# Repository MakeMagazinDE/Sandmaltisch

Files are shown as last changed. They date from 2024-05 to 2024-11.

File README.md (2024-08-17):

GitHub Logo

Maker Media GmbH

***

# Der IKEA-Hack Sandmaltisch

**Nach dem Erfahrungsbericht über den Bau des Sandtisches wollten viele Leser mehr wissen und der Ruf nach einer kompletten Bauanleitung wurde laut. Hier ist sie! Unser Autor hat keine Mühen gescheut und neben diesem Übersichtsartikel eine ausführliche Online-Schritt-für-Schritt-Anleitung, Stücklisten und CAD-Zeichnungen angefertigt.**

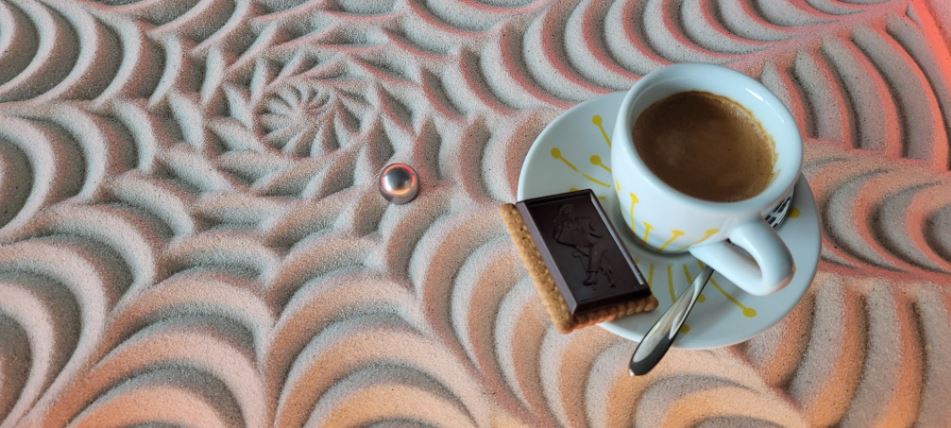
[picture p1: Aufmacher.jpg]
 

Den vollständigen Artikel gibt es in der [Make 4/24 ab Seite 16](https://www.heise.de/ratgeber/Ikea-Sandmaltisch-Bauanleitung-Teil-1-Material-und-Zusammenbau-9773244.html).

Hier finden Sie die Schritt-für-Schritt Anleitung, die 3D-Druckteile, die Firmware und GCODE-Beispielbilder.

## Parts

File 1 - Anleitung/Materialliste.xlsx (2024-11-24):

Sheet: Materialliste
IKEA Lack Sandmaltisch
Materialliste |  |  |  |  |  | 2024-11-24
Anzahl | Produkt | Total | Lieferant | Link | Hinweis | Status
1 | Makerbase MKS DLC32, ESP32 WIFI Board V2.1, inkl. zwei TMC2208 Treiber und Kühlkörper | EUR 18.00 | AliMakerstore | https://de.aliexpress.com/item/1005003246859709.html | Im Kit sind drei TMC2208-Treiber dabei. Wir brauchen nur zwei davon.
1 | Speicherkarte SD, 16 GB | EUR 5.00 | Digital-Factory Store | https://de.aliexpress.com/item/1005005834105747.html | Auf der Speicherkarte werden die GCODE-Dateien gespeichert. Geringe Anforderungen an die Speicherkapazität und Performance.
3 | Stepper Motoren NEMA17, Pancake 17HS4023, inkl. Kabel 1 Meter | EUR 15.00 | SINGRLIGOD Store | https://de.aliexpress.com/item/1005003173049902.html
2 | Limit Switches, ZW12-B | EUR 1.00 | ZHRIVOER CHINA Store | https://de.aliexpress.com/item/10000284039075.html | ZW12-B empfohlen. Bei anderen Schaltern muss sonst die Auslöseposition nachjustiert werden.
1 | Kippschalter Rocker KCD1-101 | EUR 1.00 | WGXCPP Muhao Online Store | https://de.aliexpress.com/item/1005001724551095.html | Wird für Ein-/Ausschalter verwendet.
1 | Momentary Push Button, R13-507 | EUR 1.00 | WGXCPP Muhao Online Store | https://de.aliexpress.com/item/1005001709481942.html | Wird für Reset-Schalter verwendet.
1 | 2-Pin Schraubterminal, 2.54 PCB | EUR 2.00 | E-Smartworld Store | https://de.aliexpress.com/item/1005001677869988.html | Für den Anschluss des Ein-/Ausschalters an den Controller.
2 | JST XH Stecker mit Kabel, 2 pin, 10cm | EUR 1.50 | SANDOMEY Store | https://de.aliexpress.com/item/1005001432733235.html | Für den Anschluss des Reset-Schalters an den Controller und für den Anschluss des StepDown-Converters an den 12/24-Ausgang des Controllers.
2 | JST XH Stecker mit Kabel, 3 pin, 10cm | EUR 1.50 | SANDOMEY Store | https://de.aliexpress.com/item/1005001432733235.html | Für den Anschluss der Limit Switches an den Controller.
1 | 2-Pin Kabel, AWG22, 2 Meter lang | EUR 3.00 | SkyCable Store | https://de.aliexpress.com/item/1005001732356744.html | Für den Anschluss des Ein-/Ausschalters an den Controller sowie für die Verbindung der Limit Switches mit dem Controller.
1 | Steckernetzteil, 12V, 3A, 36W, Power Jack 5.5 x 2.1mm | EUR 20.00 | (Diverse) | https://www.amazon.de/Stromversorgung-Lichtstreifen-Fernseher-Verst%C3%A4rker-Transformator-12V-3A/dp/B0BP66JZLX | Oder ein beliebiges Netzteil 12-24V, 2-3A. Möglichst langes, schwarzes Kabel empfohlen.
2 | Linearstangen zylindrisch, 8mm, 800mm, inkl. 4xLM8UU Lager | EUR 22.00 | ZHUHAI Store | https://de.aliexpress.com/item/1005001682267073.html | Von den LM8UU-Lagern werden nur 2 benötigt.
2 | Linearstangen zylindrisch, 8mm, 500mm, inkl. 4xLM8LUU Lager | EUR 21.00 | ZHUHAI Store | https://de.aliexpress.com/item/1005001682564147.html | Von den LM8LUU-Lagern werden nur 2 benötigt.
1 | GT2 Kit: 5m Zahnriemen 6mm, 2x Idler, 2x Pulleys | EUR 4.00 | SINGRLIGOD Store | https://de.aliexpress.com/item/1005003025464689.html
1 | GT2 Pulley, 20T W6 B5 | EUR 1.00 | SINGRLIGOD Store | https://de.aliexpress.com/item/1005002425542670.html
1 | GT2 Idler, 20 Zähne, 5mm Bohrung | EUR 1.00 | Big Tree Tech | https://de.aliexpress.com/item/33062594983.html
2 | GT2 Aluminium Klemmen | EUR 2.00 | Super 3D Technology | https://de.aliexpress.com/item/32813654055.html
1 | Kugel 20mm, massiv, ferromagnetisch, rostfrei | EUR 2.00 | GLT SMT Store | https://de.aliexpress.com/item/1005002787243996.html | Alternativer Lieferant aus Deutschland, liefert rostfreie, polierte Kugeln: https://tinyurl.com/5n8bmydn
1 | Neodym Scheibenmagnet mit Loch zum Anschrauben, Ø25 x 7mm, N40 | EUR 4.00 | Magnethandel.de | https://www.magnethandel.de/neodym-ringmagnete-senkung-sued-25-55-7-mm | Der Magnet sollte eine Senkbohrung von mindestens 4mm aufweisen, damit die M4-Schraube durchpasst. Eine Lieferung in die Schweiz ist leider sehr teuer. Alternativer Lieferant: Supermagnete.ch
1 | Neodym Scheibenmagnet, Ø25 x 5mm, N35 | EUR 3.00 | Magnethandel.de | https://www.magnethandel.de/neodym-magnete-25-5-mm-n35
ca. 3.5kg | Dekorsand pasteurisiert, Körnung 0.1-0.6mm | EUR 10.00 | Baumarkt, Jumbo | https://www.jumbo.ch/de/gartenbau-technik/gartenbaumaterial/gartenbodenbelaege--mauern/sand--kies--splitt/farbsand/p/4206821
1 | Moosgummimatte, 50x100cm, 2mm Stärke, schwarz | EUR 5.00 | Netco Shop | https://netco-shop.de/product_info.php?products_id=301&MODsid=ivu8c33b531trk48m20c3l3pdq
1 | IKEA Lack, Couchtisch, 90x55, schwarzbraun | EUR 30.00 | Ikea | https://www.ikea.com/ch/de/p/lack-couchtisch-schwarzbraun-40104294/
1 | Spanplatte, 884x544x12mm, roh | EUR 5.00 | Hornbach |  | Dient als Zwischenplatte.
2 | Holzplatten, MDF, 80x550x3mm, roh | EUR 1.00 | Hornbach | https://www.hornbach.de/conf/duenn-mdf-platte-einseitig-schwarz-2440x1220x3-mm-zuschnitt-online-reservierbar/3820802/ | Die Holzplatten dienen zur seitlichen Abdeckung des technischen Zwischenbaus.
2 | Holzplatten, MDF, 80x893x3mm, roh | EUR 1.00 | Hornbach | https://www.hornbach.de/conf/duenn-mdf-platte-einseitig-schwarz-2440x1220x3-mm-zuschnitt-online-reservierbar/3820802/ | Die Holzplatten dienen zur seitlichen Abdeckung des technischen Zwischenbaus.
1 | Klebefolie d-c-fix, Blackwood, 67.5x200 cm | EUR 7.00 | Hornbach | https://www.hornbach.ch/de/p/d-c-fix-klebefolie-holzdekor-blackwood-67-5x200-cm/3829390/
2 | Kanthölzer, Fichte, 44x44x670mm | EUR 9.00 | Hornbach | https://www.hornbach.ch/de/p/konsta-kantholz-fichte-gehobelt-44x44x2500-mm/1001281/ | Kann aus einem Stück Kantholz Fichte 44x44x2500mm hergestellt werden. Dienen zur Befestigung der 3D gedruckten LED- und Glasscheibenhalter.
2 | Kanthölzer, Fichte, 44x44x330mm |  |  |  | Kann aus einem Stück Kantholz Fichte 44x44x2500mm hergestellt werden. Dienen zur Befestigung der 3D gedruckten LED- und Glasscheibenhalter.
1 | LED Profil LP7, 2 Meter | EUR 20.00 | Hornbach | https://www.hornbach.ch/de/p/led-lichtprofil-set-lp7-laenge-2-m-alufarben-fuer-led-streifen/6501809/ | In vier Teile zersägen: 2 x 670mm und 2 x 330mm
1 | LED Streifen, Paulmann Entertain LED, 3m, RGB, 5V, 60 LEDs/Meter, inkl. Fernbedienung | EUR 50.00 | Hornbach | https://www.hornbach.de/p/betriebsfertiger-entertain-led-stripe-3-0-m-dynamic-rgb-farbwechsel-180-leds-mit-memoryfunktion-fernbedienung-12v/10538125/
1 | DC Power Jack Kabel, männlich, 5.5x2.5mm, Länge ca. 1 Meter | EUR 1.00 | Bolantedz Official Store | https://de.aliexpress.com/item/1005004222908762.html
1 | StepDown Converter 5V, Mini560 | EUR 1.00 | TULX Global Store | https://de.aliexpress.com/item/1005004114708195.html
4 | LED Verbinder, 4 Pin, 10mm, double | EUR 2.00 | Loamlin Official Store | https://de.aliexpress.com/item/1005001521762588.html | Die Breite dieser Stecker ist 14.5mm. Breiter dürfen die Stecker keinesfalls sein!
1 | Sicherheitsglas ESG, 6mm Stärke, Kanten gesäumt | EUR 100.00 | Lokaler Glashändler oder Baumarkt | https://www.jumbo.ch/de/bauen-renovieren/glas-kunstglas/kunstglas/einscheibensicherheitsglas-esg-6-mm/p/5840845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 | Die genauen Abmessungen ergeben sich im Verlaufe des Projekts, siehe Anleitung (Richtwert: 418x768mm). Nach Möglichkeit "extraweiss" bestellen (ohne Grünstich).
1 | Saugnapf | EUR 2.00 | Homast Store | https://de.aliexpress.com/item/1005004833801393.html | Optional. Damit kann die Glasplatte aus der Versenkung gehoben werden.
 | Filament, PLA oder PETG, schwarz, ca. 1.2 kg | EUR 40.00
 | Kleinteile gemäss Register "Schrauben und Muttern" | EUR 30.00
 | Holzleim
 | Schrumpfschlauch
 | Isolierband
 | Schleifpapier grob
 |  | EUR 443.00

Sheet: Schrauben und Muttern
IKEA Lack Sandmaltisch
Schrauben und Muttern
Verbindung | Anzahl | Artikel | Abmessung | Empfehlung Kopf | Hinweis
Abdeckung an Eckteile | 8 | Metallschrauben, M3x10, schwarz, Ultraflachkopf | M3x10 | Ultraflachkopf | Schwarz und Flachkopf empfohlen, da sichtbare Schraube.
Abdeckung an Eckteile | 8 | Unterlegscheiben, M3x10, schwarz | M3x10 |  | Schwarz empfohlen, da sichtbare Unterlegscheibe.
Abdeckung an Eckteile | 8 | Gewindeeinsätze, M3xL5xOD4.5 | M3x5x4.5
Controller-Box: Rahmen an Controller-Boden | 2 | Metallschrauben, M3x10, schwarz, Ultraflachkopf | M3x10 | Ultraflachkopf | Als Achse für den Klapp-Mechanismus der Box.
Controller-Box: Rahmen an Controller-Boden | 1 | Gewindeeinsätze, M3xL5xOD4.5 | M3x5x4.5 |  | Für die Arretierung beim Auf-/Zuklappen.
Controller-Box: Rahmen an Controller-Boden | 1 | Metallschrauben, M3x6 | M3x6 |  | Für die Arretierung beim Auf-/Zuklappen.
Makerbase-Board in Controller-Box | 4 | Metallschrauben, M3x6 | M3x6 | Zylinder
Makerbase-Board in Controller-Box | 4 | Gewindeeinsätze, M3xL5xOD4.5 | M3x5x4.5
Controller-Box Rahmen an Zwischenplatte | 4 | Holzschrauben, 3x12, Senkkopf | 3x12 | Senkkopf | Schrauben sollten keinesfalls länger als 14mm sein.
Zwischenplatte an Tischbeine | 4 | Metallschraube, M6x50, Flachkopf | M6x50 | Flachrundkopf
Zwischenplatte an Tischbeine | 4 | Unterlegscheiben, M6x18x1.5 | M6x18
Eckteile an Verstrebungen | 8 | Metallschrauben, M5x25, Aussensechskant | M5x25 | Sechskant aussen
Eckteile an Verstrebungen | 8 | Unterlegscheiben M5x15x1 | M5x15x1
Eckteile an Verstrebungen | 8 | Sechskantmuttern, M5 | M5
Tischbeine an Verstrebungen | 4 | Holzschrauben, 3x12, Senkkopf | 3x12 | Senkkopf
Tischplatte mit Eckteilen | 4 | Gewindestift, M6x50, Innensechskant | M6x50 | Innensechskant | Diese Gewindestifte mit Innensechskant lassen sich mit einem Inbusschlüssel sehr gut einschrauben.
Tischplatte mit Eckteilen | 4 | Sechskantmuttern, M6 | M6
Tischplatte mit Eckteilen | 4 | Unterlegscheiben, M6x18x1.5 | M6x18
LED Profil-Halter an Rechteckleisten | 20 | Holzschrauben, 3x12, Senkkopf | 3x12 | Senkkopf
Y-Linearstangen an Anschlag-Plättchen | 2 | Gewindeeinsätze, M3xL5xOD4.5 | M3x5x4.5
Y-Linearstangen an Anschlag-Plättchen | 2 | Metallschrauben, M3x10 | M3x10 | Zylinder
Y-Linearstangen an Anschlag-Schraube | 2 | Metallschrauben, M3x10 | M3x10 | Zylinder
Montage NEMA17 Motor, X-Achse (Y-Schlitten) | 4 | Metallschrauben, M3x6 | M3x6 | Zylinder
Montage NEMA17 Motoren, Y-Achse | 6 | Metallschrauben, M3x6 | M3x6 | Zylinder | Drei Schrauben pro NEMA-Motor.
Montage GT2 Idler (X- und Y-Achsen) | 3 | Metallschrauben, M5x25, Ultraflachkopf | M5x25
Montage GT2 Idler X-Achse | 1 | Unterlegscheiben M5x15x1 | M5x15x1
Montage Lager auf Y-Achse mit Klemme | 8 | Metallschrauben, M3x10 | M3x10 | Zylinder
Montage Lager auf Y-Achse mit Klemme | 8 | Gewindeeinsätze, M3xL5xOD4.5 | M3x5x4.5
Arretierung Zahnriemen Y-Achsen mit Klemme | 2 | Metallschrauben, M3x10 | M3x10 | Zylinder
Arretierung Zahnriemen Y-Achsen mit Klemme | 2 | Gewindeeinsätze, M3xL5xOD4.5 | M3x5x4.5
Arretierung Zahnriemen Y-Achsen mit Schraube | 2 | Metallschrauben, M3x10 | M3x10 | Zylinder
Arretierung Zahnriemen Y-Achsen mit Schraube | 2 | Gewindeeinsätze, M3xL5xOD4.5 | M3x5x4.5
Montage Lager auf X-Achse mit Klemme | 2 | Metallschrauben, M3x20 | M3x20 | Zylinder
Montage Lager auf X-Achse mit Klemme | 2 | Gewindeeinsätze, M3xL5xOD4.5 | M3x5x4.5
Arretierung Zahnriemen X-Achse | 2 | Metallschrauben, M3x20 | M3x20 | Zylinder
Arretierung Zahnriemen X-Achse | 2 | Gewindeeinsätze, M3xL5xOD4.5 | M3x5x4.5
Montage Scheibenmagnet | 1 | Metallschrauben, M4x14, Senkkopf | M4x14 | Senkkopf | Senkkopf zwingend!
Montage Limit Schalter | 4 | Metallschrauben, M2.5x10 | M2.5x10 | Zylinder
Montage LED Kabel mit Kabelclips | 2 | Holzschrauben, 3x12, Senkkopf | 3x12 | Senkkopf
Ergebnis | 167
Total Schrauben und Muttern: | Anzahl | Link | AliExpress Shop | Status
Gewindeeinsätze, M3xL5xOD4.5 | 31 | https://de.aliexpress.com/item/1005006071488810.html | Edgar Gary
Gewindestift, M6x50, Innensechskant | 4 | https://de.aliexpress.com/item/1005003114146413.html | Haiking
Holzschrauben, 3x12, Senkkopf | 30 | https://de.aliexpress.com/item/1005002914051799.html | Zonsta
Metallschraube, M6x50, Flachkopf | 4 | https://de.aliexpress.com/item/1005004510618943.html | Haiking
Metallschrauben, M2.5x10 | 4 | https://de.aliexpress.com/item/1005004510631911.html | Haiking
Metallschrauben, M3x6 | 15 | https://de.aliexpress.com/item/1005003116411038.html | Haiking
Metallschrauben, M3x10, schwarz, Ultraflachkopf | 10 | https://de.aliexpress.com/item/1005004510624216.html | Haiking
Metallschrauben, M3x10 | 16 | https://de.aliexpress.com/item/1005003116411038.html | Haiking
Metallschrauben, M3x20 | 4 | https://de.aliexpress.com/item/1005003116557759.html | Haiking
Metallschrauben, M4x14, Senkkopf | 1 | https://de.aliexpress.com/item/1005004510637802.html | Haiking
Metallschrauben, M5x25, Ultraflachkopf | 3 | https://de.aliexpress.com/item/1005004510603548.html | Haiking
Metallschrauben, M5x25, Aussensechskant | 8 | https://de.aliexpress.com/item/1005003114095405.html | Haiking
Sechskantmuttern, M5 | 8 | https://de.aliexpress.com/item/1005003111431468.html | Haiking
Sechskantmuttern, M6 | 4 | https://de.aliexpress.com/item/1005003111431468.html | Haiking
Unterlegscheiben, M3x10, schwarz | 8 | https://de.aliexpress.com/item/1005003212029031.html | Blazingstar
Unterlegscheiben M5x15x1 | 9 | https://de.aliexpress.com/item/1005003226049975.html | Blazingstar
Unterlegscheiben, M6x18x1.5 | 8 | https://de.aliexpress.com/item/1005003226049975.html | Blazingstar
Summe | 167
Allgemeine Hinweise
Preis für alle Schrauben/Muttern insgesamt ca. 30 Euro.

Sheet: Druckbare Bauteile
IKEA Lack Sandmaltisch
Druckbare Bauteile
3MF-Datei | Druckzeit (h) | Gewicht (g) | Sichtbar | Filament | Hinweis
Verstrebungen.3mf | 1.30 | 36 | Ja | PLA Schwarz
Eckteile.3mf | 11.75 | 336 | Nein | PLA Rot
Tischbeinabdeckungen.3mf | 1.50 | 47 | Ja | PLA Schwarz
Kabelkanal.3mf | 1.00 | 26 | Nein | PLA Rot
Controller Box-Rahmen.3mf | 1.60 | 68 | Ja | PLA Schwarz
Controller Box-Boden.3mf | 2.00 | 76 | Ja | PLA Schwarz
Y-Schlitten.3mf | 3.50 | 64 | Nein | PLA Rot
X-Schlitten.3mf | 0.75 | 14 | Nein | PLA Rot
LED Profil-HalterEcken.3mf | 7.75 | 138 | Ja | PLA Schwarz
LED Profil-HalterStandard.3mf | 16.50 | 321 | Ja | PLA Schwarz | 3mf-Datei dreimal drucken (12 Stück)
LED Profil-Blenden.3mf | 0.75 | 16 | Ja | PLA Schwarz
Werkzeuge.3mf | 1.00 | 36 | Nein | PLA Blau
Kabelclip.3mf | 0.1 | 1 | Ja | PLA Schwarz
 | 49.50 | 1179

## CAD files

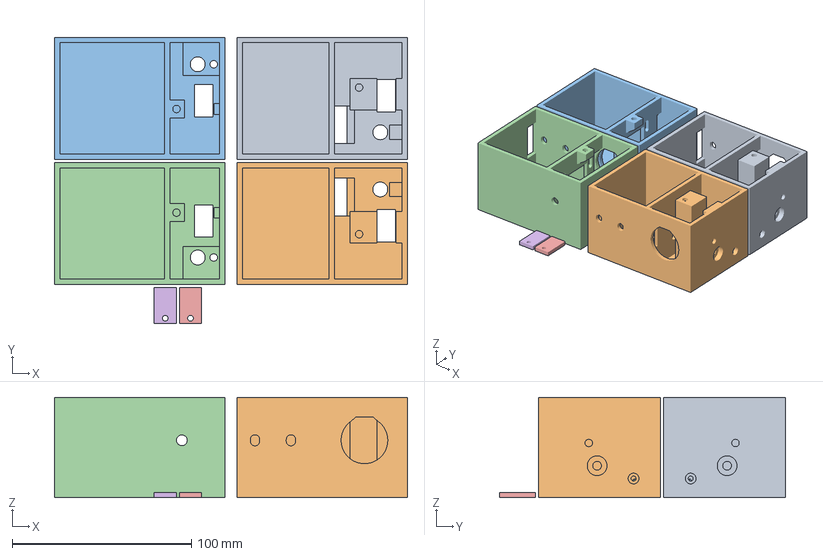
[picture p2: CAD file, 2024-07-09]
2 - 3D Druck/3MF-Dateien/Eckteile.3mf
196.8 x 159.6 x 56.0 mm
Eckteil 1-UntenLinks.stl
Eckteil 2-UntenRechts.stl
Eckteil 3-ObenLinks.stl
Eckteil 4-ObenRechts.stl
AnschlagZylinderstange.stl

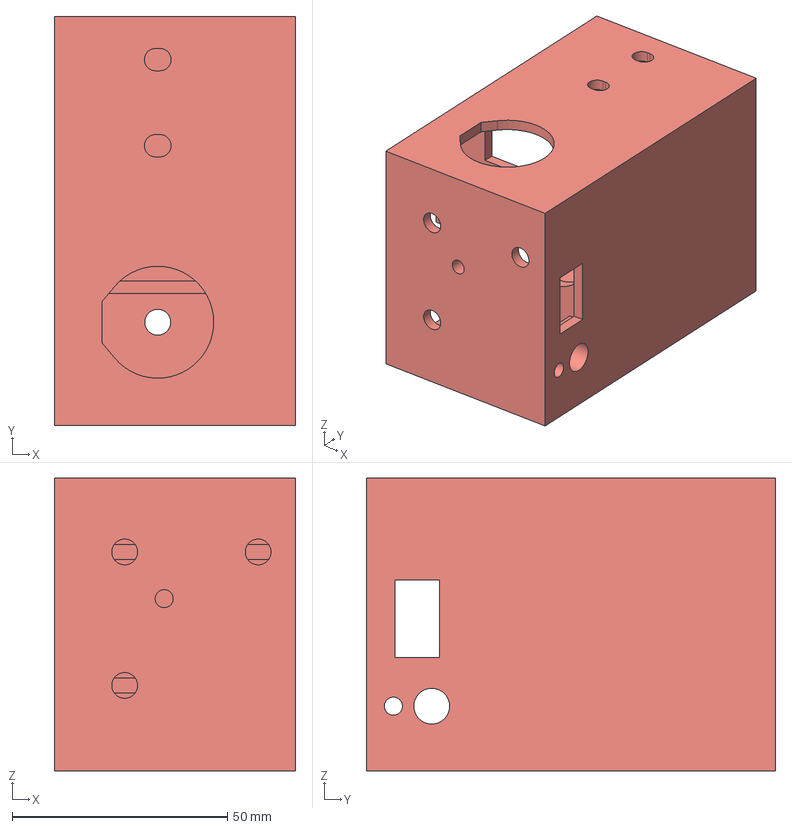
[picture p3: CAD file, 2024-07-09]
2 - 3D Druck/STEP-Dateien/Eckteil 4-ObenRechts.step
56.0 x 95.0 x 68.0 mm

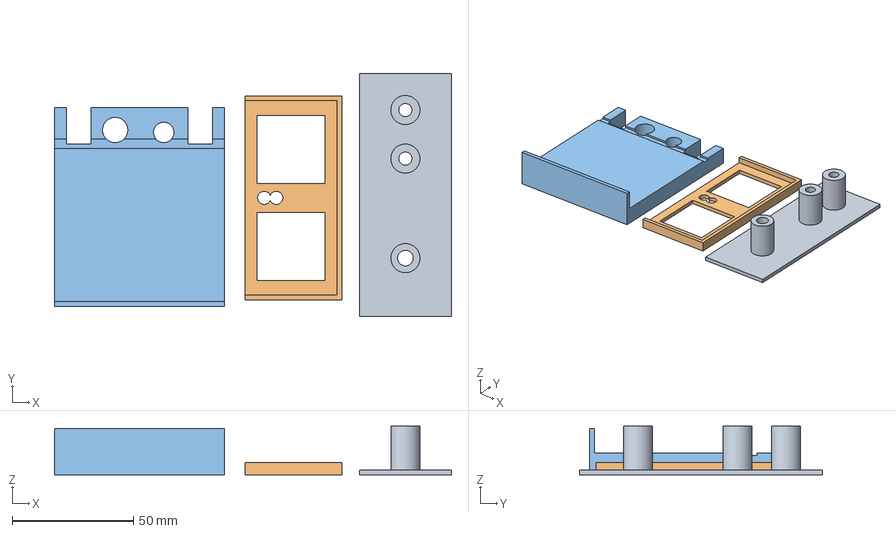
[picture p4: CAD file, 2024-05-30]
2 - 3D Druck/3MF-Dateien/Werkzeuge.3mf
163.5 x 100.0 x 20.0 mm
Bohrschablone Zwischenplatte.stl
Bohrschablone Abdeckung.stl
BohrschabloneLinealVollausschnitt.stl

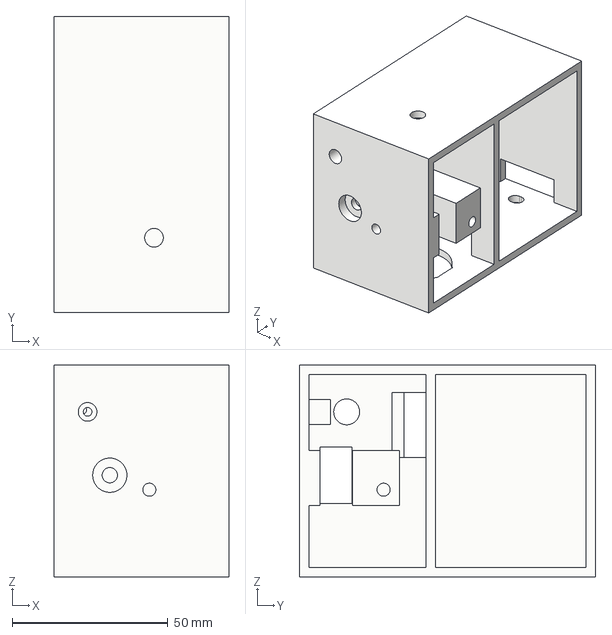
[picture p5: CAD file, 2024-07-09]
2 - 3D Druck/STEP-Dateien/Eckteil 1-UntenLinks.step
56.0 x 95.0 x 68.0 mm

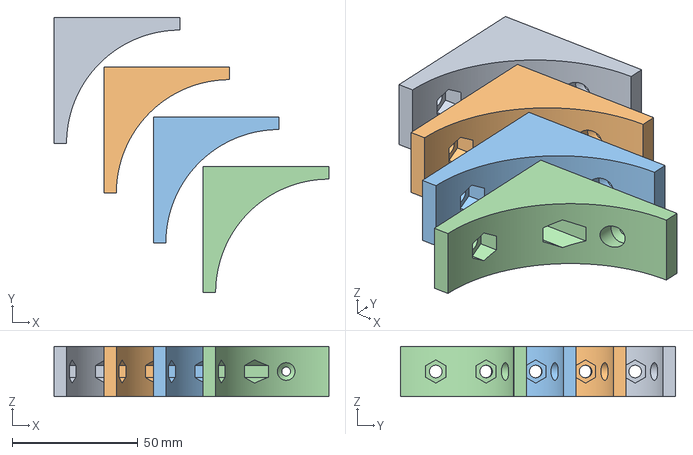
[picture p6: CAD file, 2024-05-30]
2 - 3D Druck/3MF-Dateien/Verstrebungen.3mf
109.2 x 109.2 x 20.0 mm

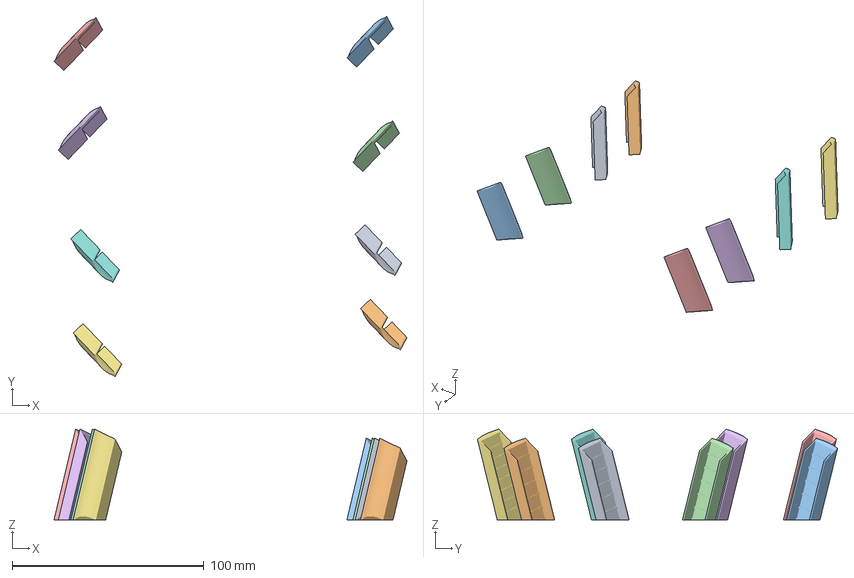
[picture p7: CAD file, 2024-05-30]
2 - 3D Druck/3MF-Dateien/LED Profil-Blenden.3mf
183.9 x 187.8 x 47.3 mm
LED ProfilBlende-EckeKurz1.stl
LED ProfilBlende-EckeKurz2.stl
LED ProfilBlende-EckeLang1.stl
LED ProfilBlende-EckeLang2.stl

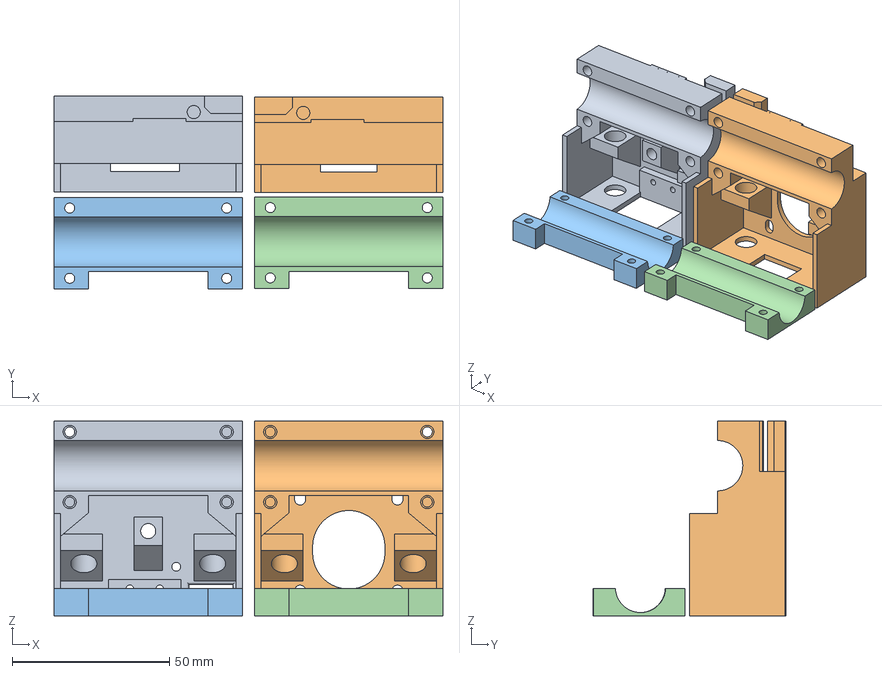
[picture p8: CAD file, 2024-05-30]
2 - 3D Druck/3MF-Dateien/Y-Schlitten.3mf
123.9 x 61.4 x 61.9 mm
Y-Schlitten 1-Links.stl
Y-Schlitten 2-Rechts.stl
Y-Schlitten-Klemme.stl

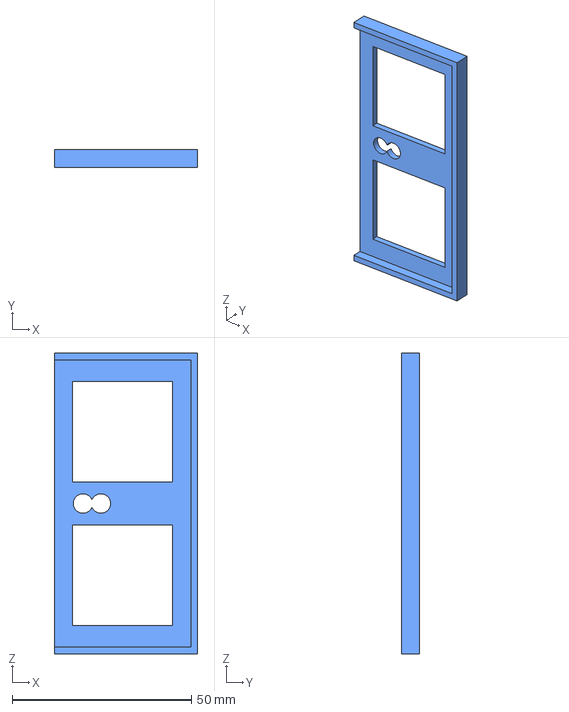
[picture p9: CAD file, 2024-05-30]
2 - 3D Druck/STEP-Dateien/Bohrschablone Abdeckung.step
40.0 x 5.00 x 84.0 mm

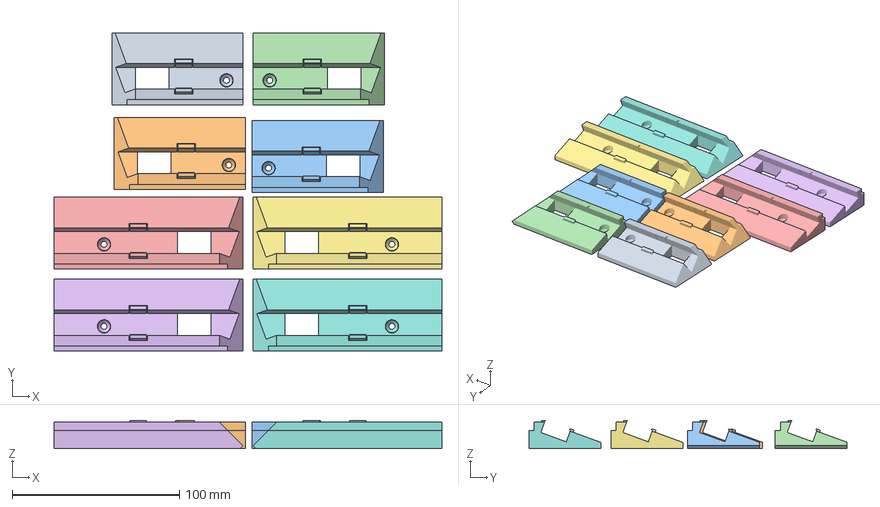
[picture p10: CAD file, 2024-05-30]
2 - 3D Druck/3MF-Dateien/LED Profil-HalterEcken.3mf
231.8 x 190.2 x 16.9 mm
LED Profil-HalterEckeKurz1.stl
LED Profil-HalterEckeKurz2.stl
LED Profil-HalterEckeLang1.stl
LED Profil-HalterEckeLang2.stl

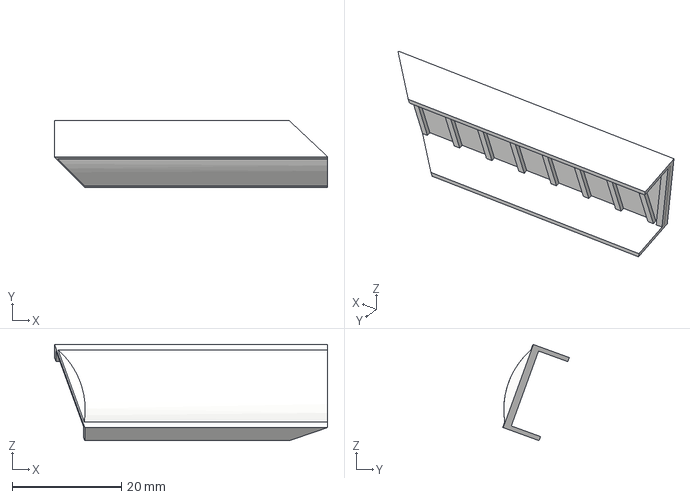
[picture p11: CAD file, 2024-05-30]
2 - 3D Druck/STEP-Dateien/LED ProfilBlende-EckeLang2.step
50.0 x 12.2 x 17.7 mm

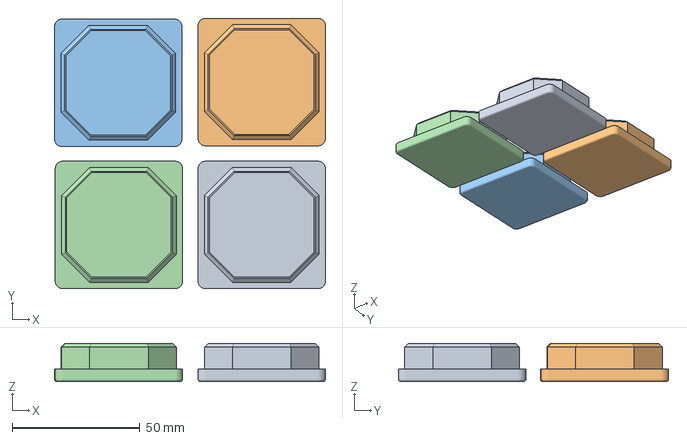
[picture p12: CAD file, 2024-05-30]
2 - 3D Druck/3MF-Dateien/Tischbeinabdeckungen.3mf
106.3 x 106.0 x 15.0 mm

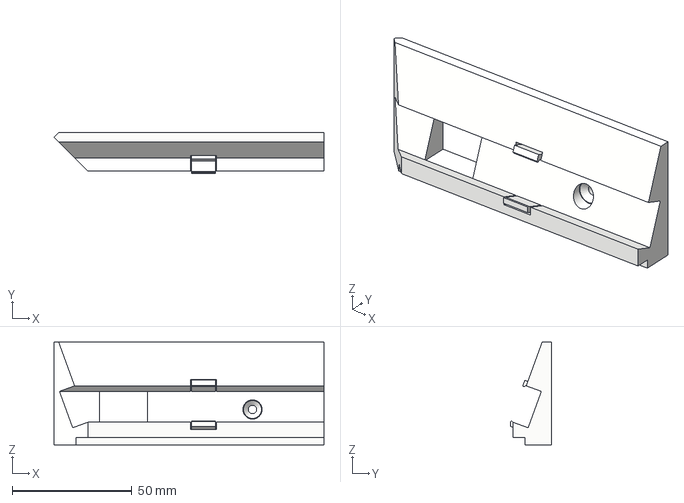
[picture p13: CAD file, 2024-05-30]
2 - 3D Druck/STEP-Dateien/LED Profil-HalterEckeLang2.step
112.9 x 16.9 x 43.0 mm

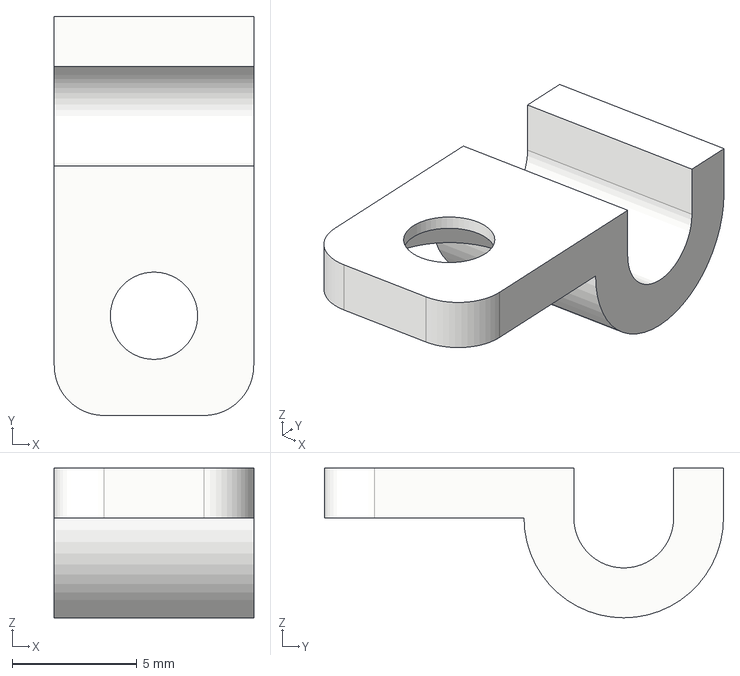
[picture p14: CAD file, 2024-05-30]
2 - 3D Druck/STEP-Dateien/Kabelclip.step
8.00 x 16.0 x 6.00 mm

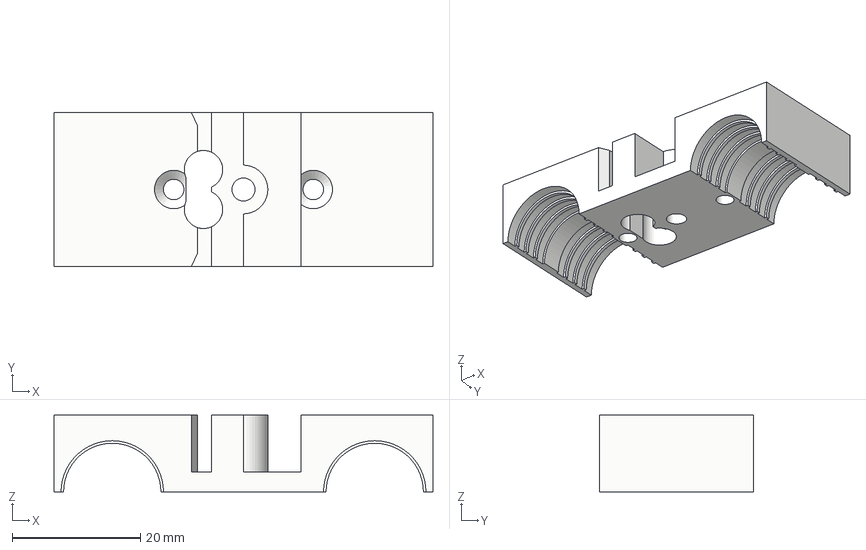
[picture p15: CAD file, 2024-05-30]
2 - 3D Druck/STEP-Dateien/X-Schlitten.step
59.2 x 24.0 x 12.0 mm

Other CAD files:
2 - 3D Druck/STEP-Dateien/Eckteil 2-UntenRechts.step
2 - 3D Druck/STEP-Dateien/Eckteil 3-ObenLinks.step
2 - 3D Druck/STEP-Dateien/LED Profil-HalterEckeLang1.step
2 - 3D Druck/STEP-Dateien/LED ProfilBlende-EckeKurz2.step
2 - 3D Druck/3MF-Dateien/Controller Box-Boden.3mf
2 - 3D Druck/3MF-Dateien/Controller Box-Rahmen.3mf
2 - 3D Druck/3MF-Dateien/Kabelclip.3mf
2 - 3D Druck/3MF-Dateien/Kabelkanal.3mf
2 - 3D Druck/3MF-Dateien/LED Profil-HalterStandard.3mf
2 - 3D Druck/3MF-Dateien/X-Schlitten.3mf
2 - 3D Druck/STEP-Dateien/AnschlagZylinderstange.step
2 - 3D Druck/STEP-Dateien/Bohrschablone Zwischenplatte.step
2 - 3D Druck/STEP-Dateien/BohrschabloneLinealVollausschnitt.step
2 - 3D Druck/STEP-Dateien/Controller Box-Boden.step
2 - 3D Druck/STEP-Dateien/Controller Box-Rahmen.step
2 - 3D Druck/STEP-Dateien/Kabelkanal.step
2 - 3D Druck/STEP-Dateien/LED Profil-HalterEckeKurz1.step
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

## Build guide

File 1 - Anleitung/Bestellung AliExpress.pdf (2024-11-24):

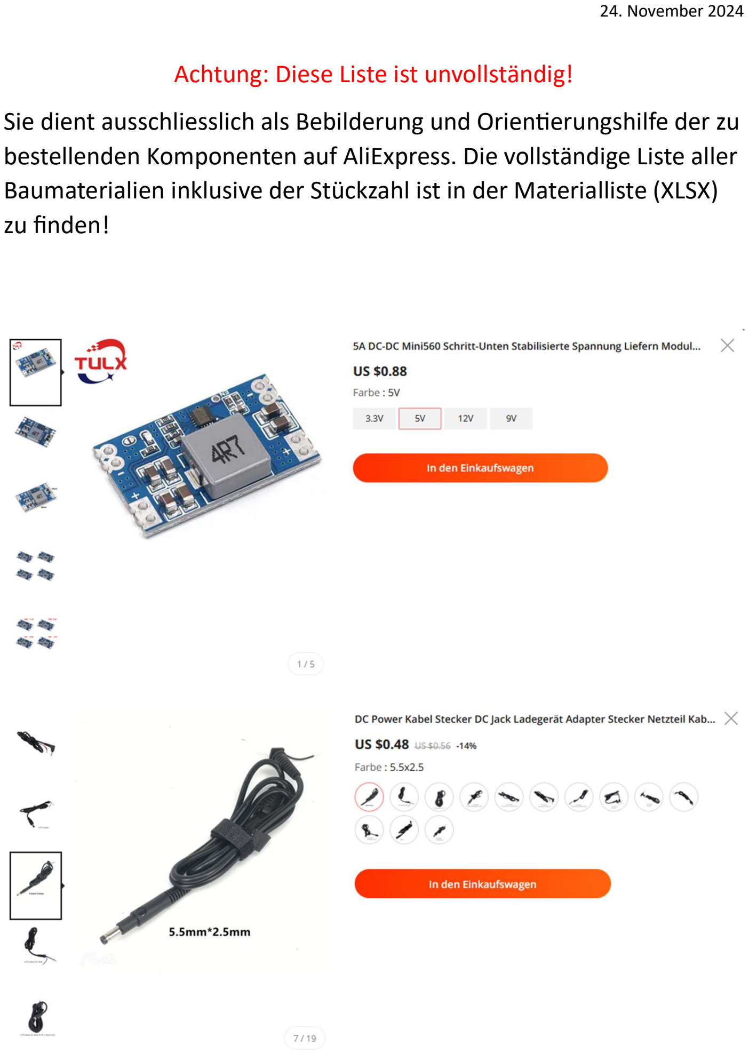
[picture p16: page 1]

### 24. November 2024

Achtung: Diese Liste ist unvollständig! Sie dient ausschliesslich als Bebilderung und Orienerungshilfe der zu bestellenden Komponenten auf AliExpress. Die vollständige Liste aller Baumaterialien inklusive der Stückzahl ist in der Materialliste (XLSX) zu finden!

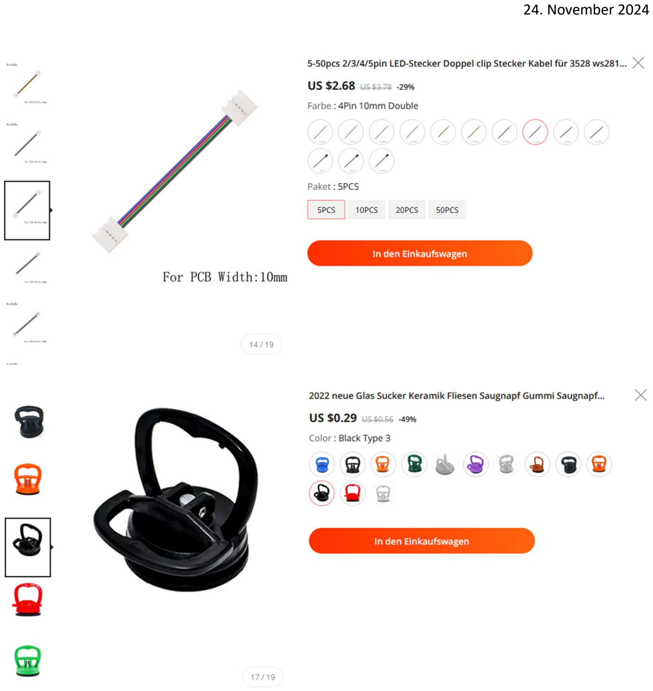
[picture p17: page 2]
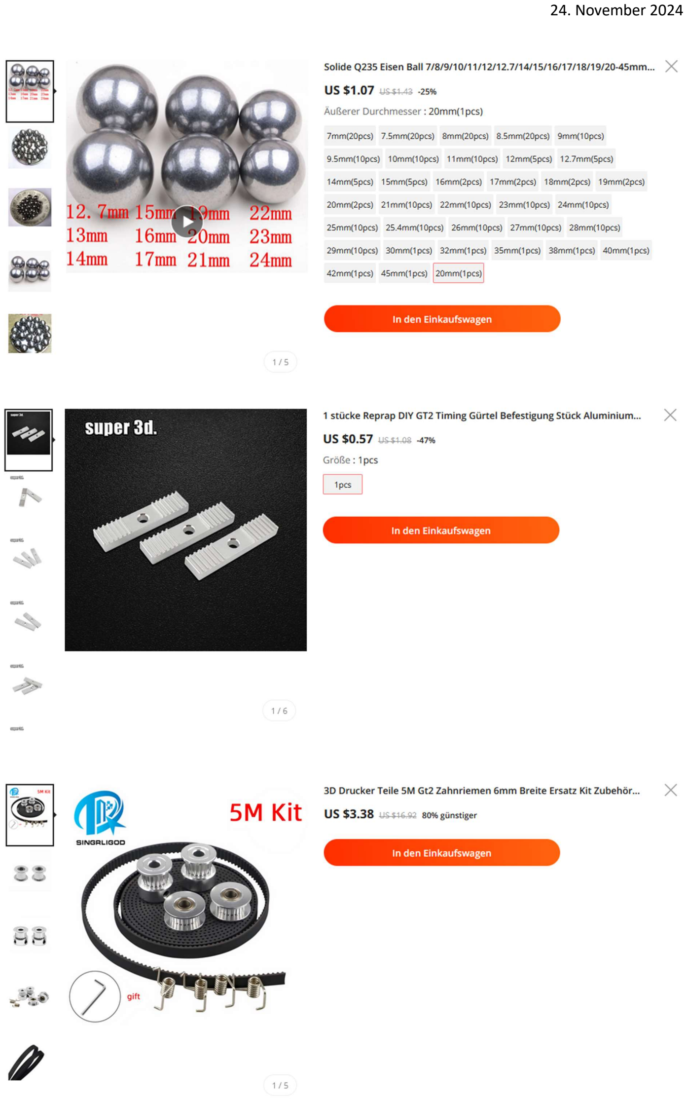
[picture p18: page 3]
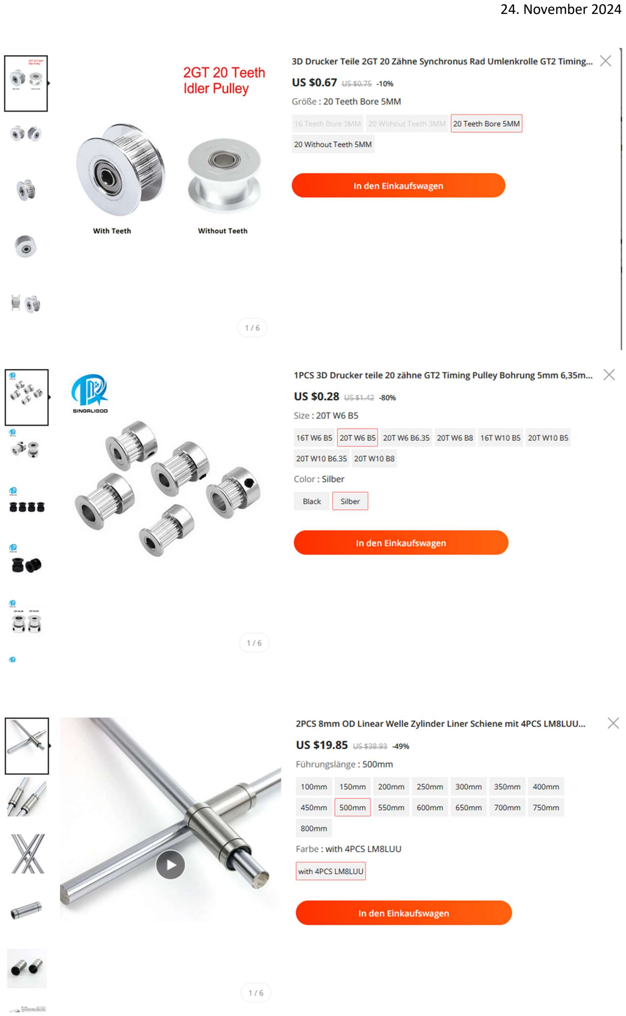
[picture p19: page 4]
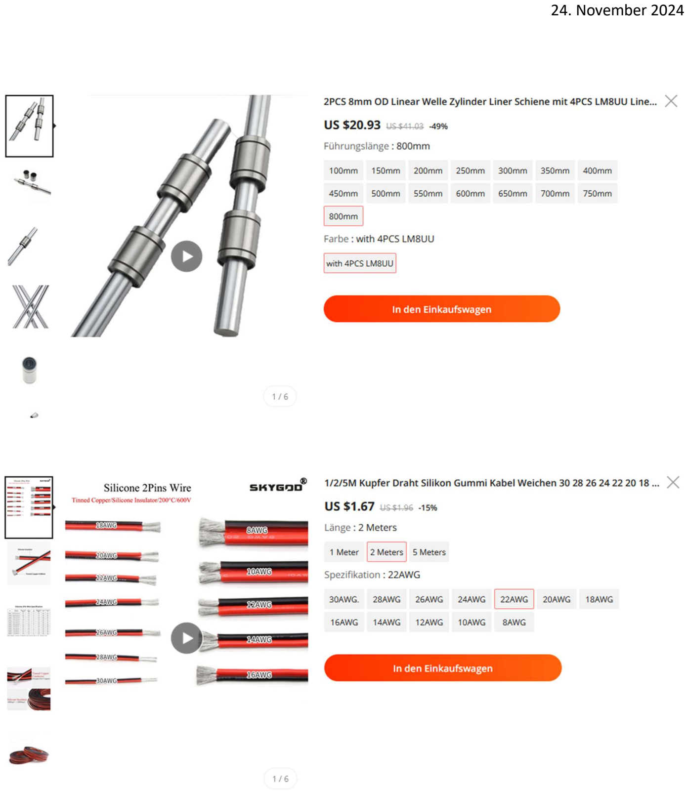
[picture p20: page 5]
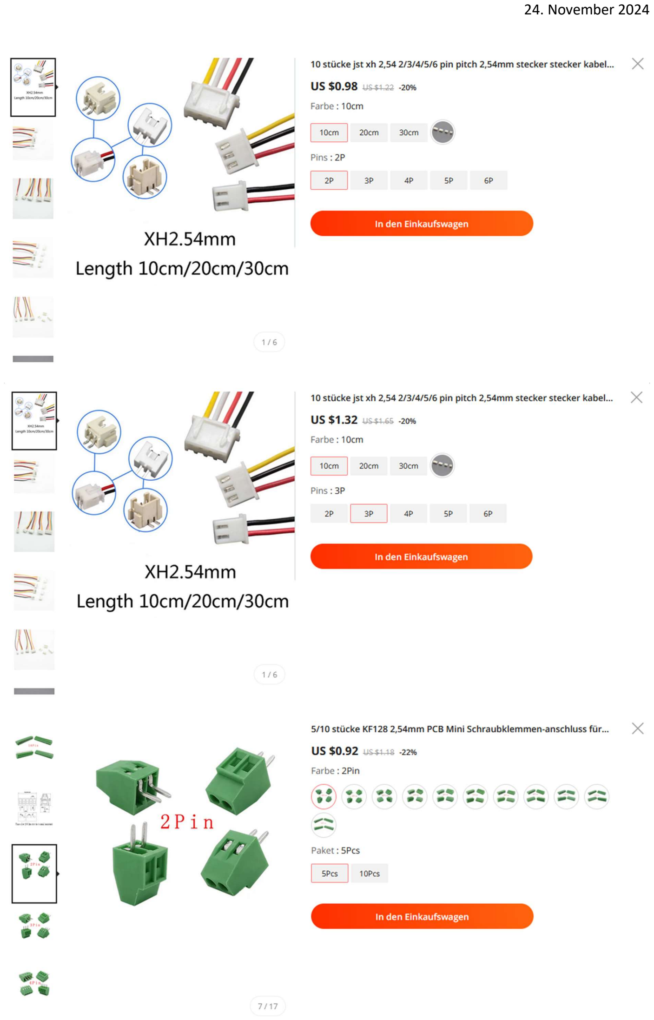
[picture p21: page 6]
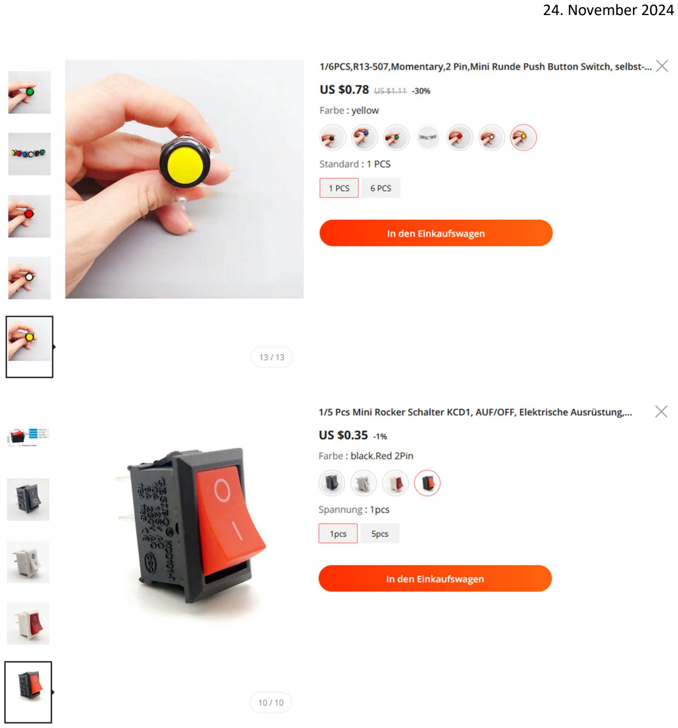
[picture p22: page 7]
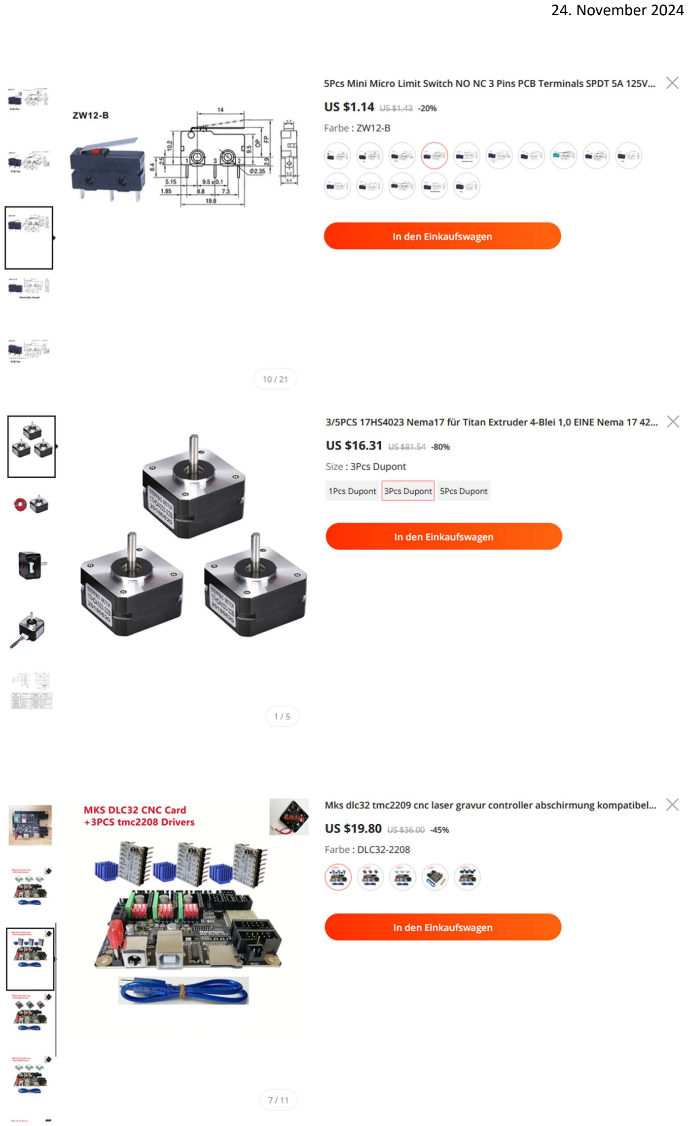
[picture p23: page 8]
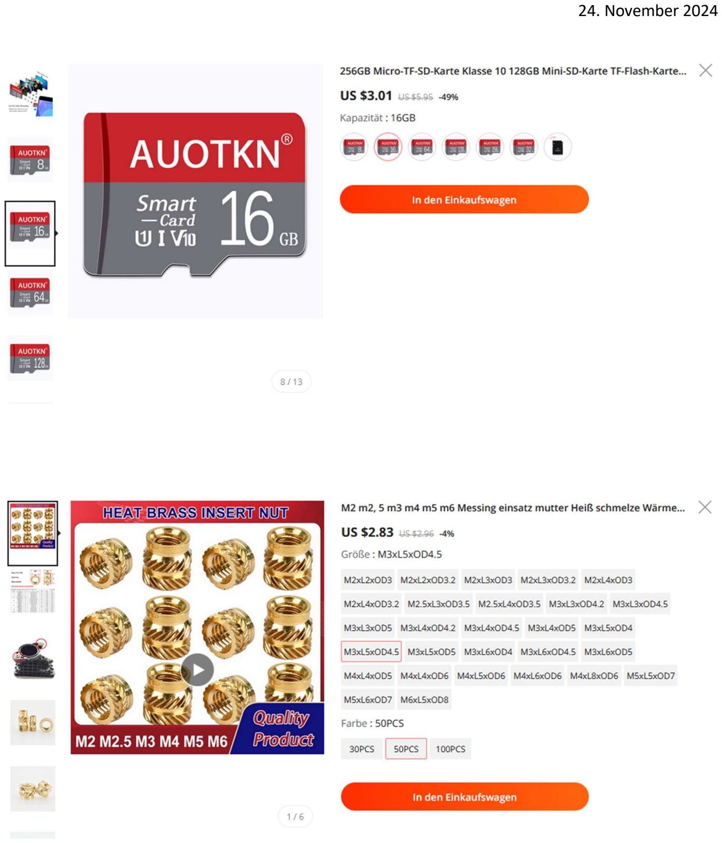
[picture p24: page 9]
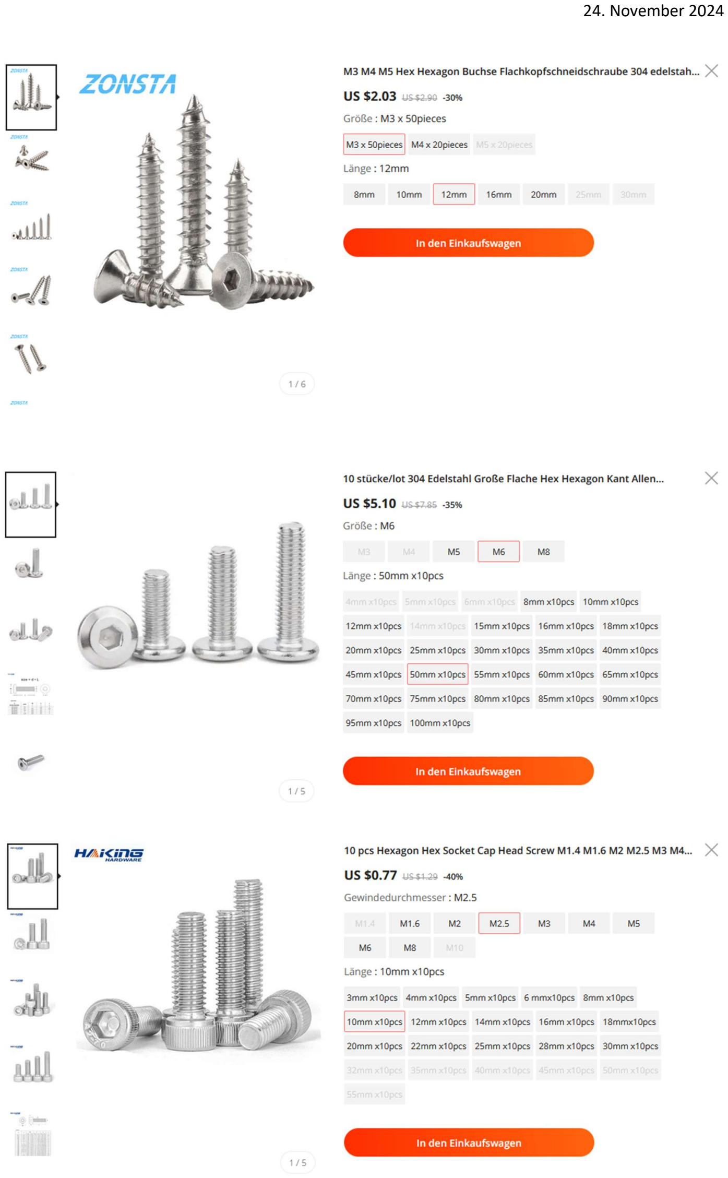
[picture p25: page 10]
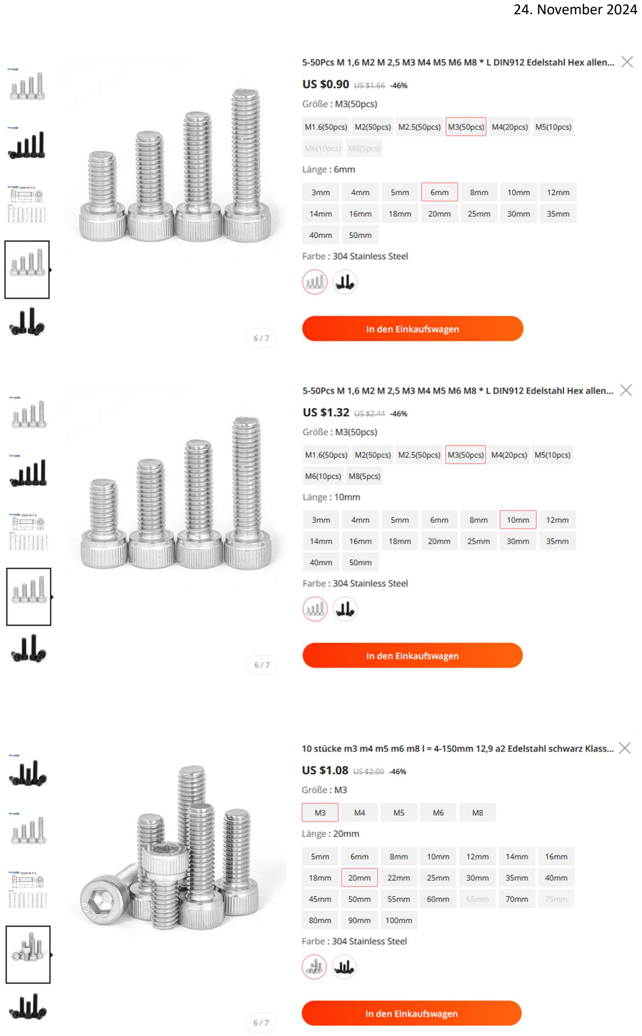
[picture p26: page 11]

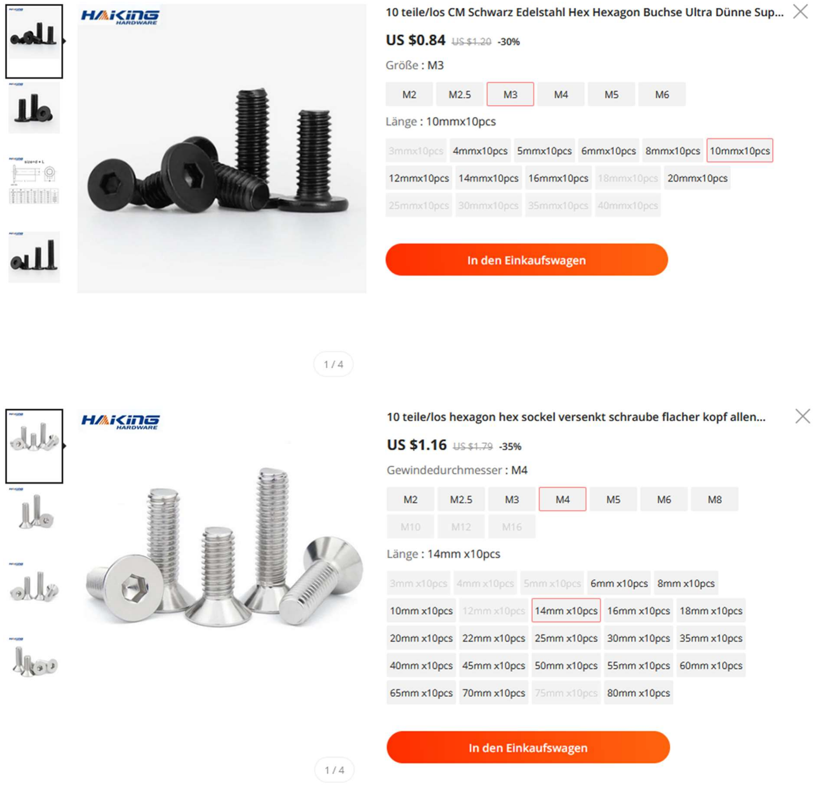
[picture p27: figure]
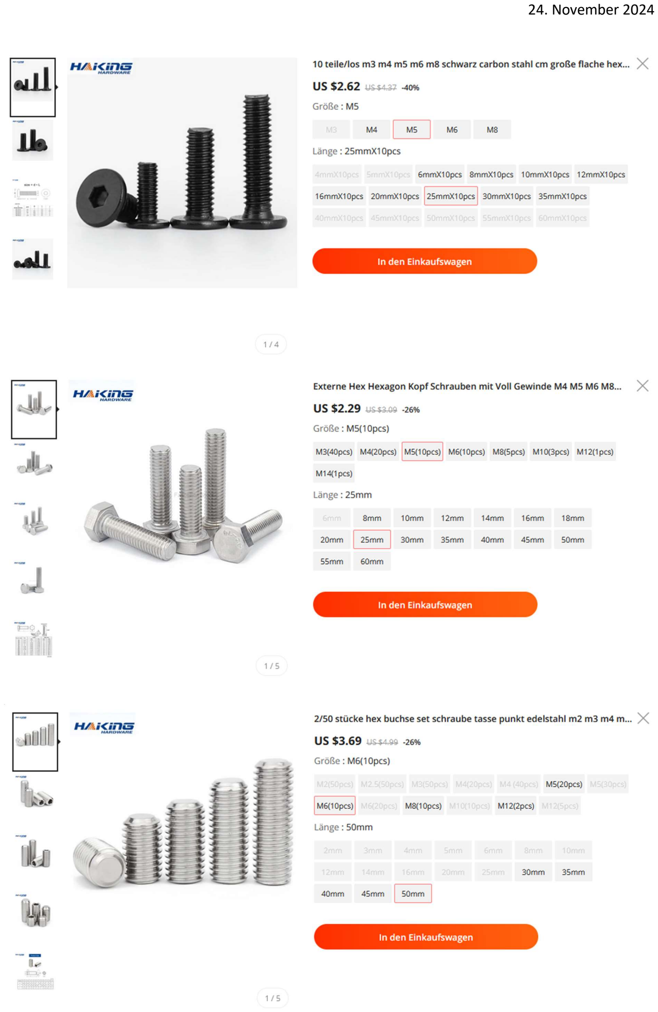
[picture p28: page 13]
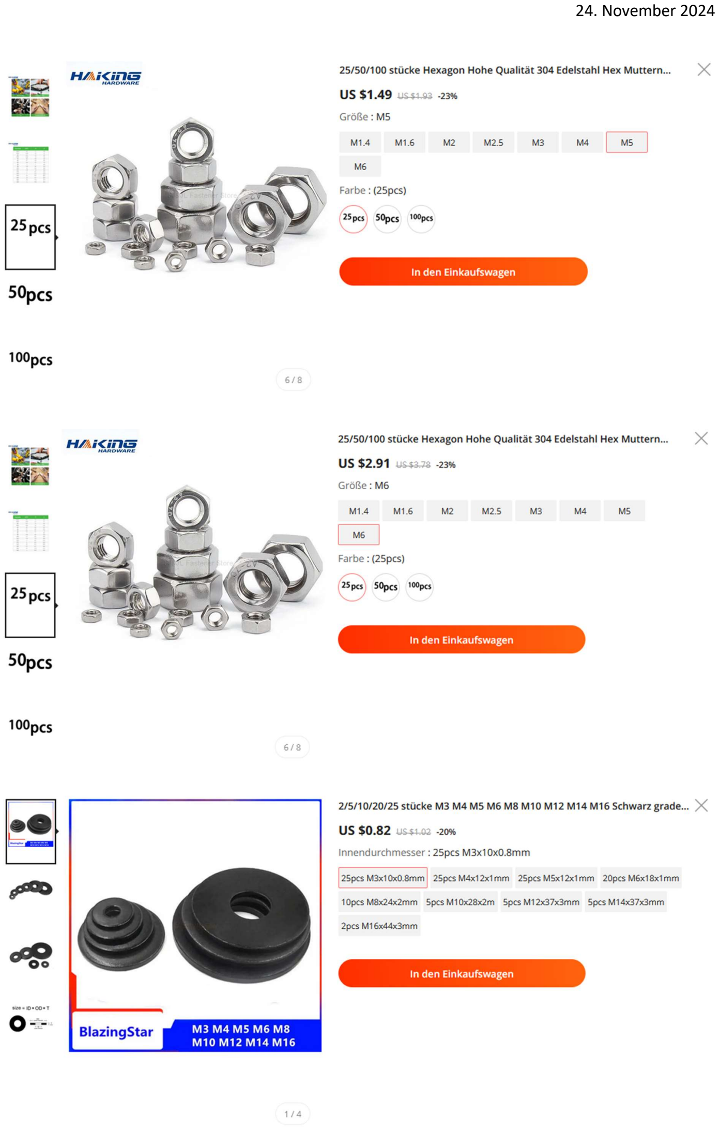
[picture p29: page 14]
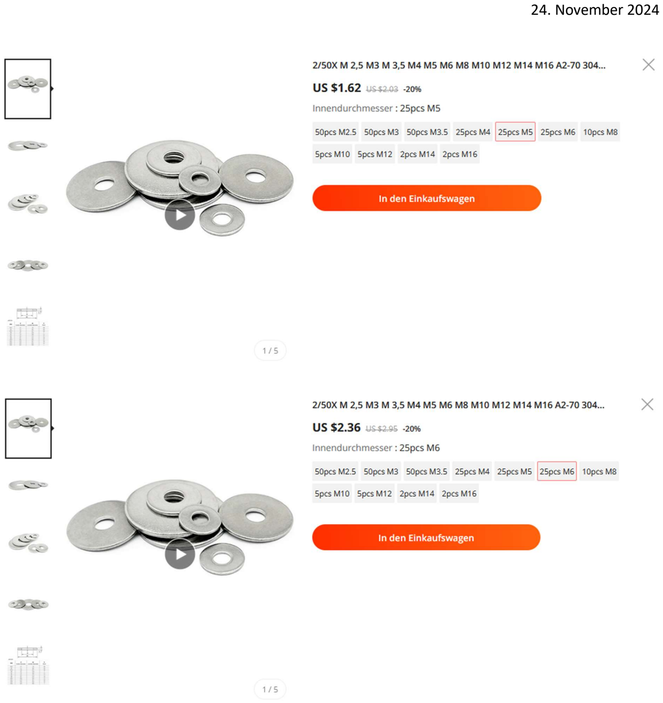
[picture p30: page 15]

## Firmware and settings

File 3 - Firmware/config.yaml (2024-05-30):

board: MKS-DLC32 V2.1
name: BINGOBRICKS Sandmaltisch
meta: 17.4.2024 - MAKE Magazin

kinematics:
  Cartesian:

stepping:
  engine: I2S_STATIC
#Static only, Stream Produces a second "ghost line" when doing engraving/Filling
  idle_ms: 5
  pulse_us: 10
  dir_delay_us: 1
  disable_delay_us: 0
axes:
  shared_stepper_disable_pin: I2SO.0
  x:
    steps_per_mm: 40
    max_rate_mm_per_min: 3000
    acceleration_mm_per_sec2: 500
    max_travel_mm: 388
    soft_limits: true
    homing:
      cycle: 1
      positive_direction: false
      mpos_mm: 0
      feed_mm_per_min: 100
      seek_mm_per_min: 1000

      settle_ms: 500
      seek_scaler: 1.1
      feed_scaler: 1.1

    motor0:
      limit_neg_pin: gpio.36:low
      hard_limits: false
      pulloff_mm: 2
      stepstick:
        step_pin: I2SO.1
        direction_pin: I2SO.2:high

  y:
    steps_per_mm: 40
    max_rate_mm_per_min: 3000
    acceleration_mm_per_sec2: 500
    max_travel_mm: 718
    soft_limits: true
    homing:
      cycle: 1
      positive_direction: false
      mpos_mm: 0
      feed_mm_per_min: 100
      seek_mm_per_min: 1000
      settle_ms: 500
      seek_scaler: 1.100
      feed_scaler: 1.100

    motor0:
      limit_neg_pin: gpio.35:low
      hard_limits: false
      pulloff_mm: 2
      stepstick:
        step_pin: I2SO.5
        direction_pin: I2SO.6:low

  z: none

i2so:
  bck_pin: gpio.16
  data_pin: gpio.21
  ws_pin: gpio.17

spi:
  miso_pin: gpio.12
  mosi_pin: gpio.13
  sck_pin: gpio.14

sdcard:
  cs_pin: gpio.15
  card_detect_pin: gpio.39

control:
  safety_door_pin: NO_PIN
  reset_pin: NO_PIN
  feed_hold_pin: NO_PIN
  cycle_start_pin: NO_PIN
  macro0_pin: gpio.33:low:pu
  macro1_pin: NO_PIN
  macro2_pin: NO_PIN
  macro3_pin: NO_PIN

macros:
  startup_line0:
  startup_line1:

coolant:
  flood_pin: NO_PIN
  mist_pin: NO_PIN
  delay_ms: 0

probe:
  pin: gpio.22
  check_mode_start: true

Laser:
  pwm_hz: 5000
#For software PWM control on K40, IN on TTL connection, G next to IN to G on TTL. No need for Enable
  output_pin: gpio.32
  enable_pin: NO_PIN
  disable_with_s0: false
  s0_with_disable: false
  tool_num: 0
  speed_map: 0=7.500% 2200=100.000%
# 165=1mA (not enough to fire), 880=9mA 2200=16mA
# Set your own MAX and Minimum,
# Change max until desired MAX mA on gauge
# Change min until laser just before laser fires.

user_outputs:
  analog0_pin: NO_PIN
  analog1_pin: NO_PIN
  analog2_pin: NO_PIN
  analog3_pin: NO_PIN
  analog0_hz: 5000
  analog1_hz: 5000
  analog2_hz: 5000
  analog3_hz: 5000
  digital0_pin: NO_PIN
  digital1_pin: NO_PIN
  digital2_pin: NO_PIN
  digital3_pin: NO_PIN

start:
  must_home: false

# 5,18,19,22,23,25,26,27,32,33,39,I2SO.7
# SDA 0 / SCL 4

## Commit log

2024-05-31 Add files via upload
    Leicht aktualisierte Version der Bauanleitung: Die Moosgummimatte sollte nicht eingeklebt, sondern nur eingelegt werden.
2024-07-09 Letzte Updates
    Optimierungen
    [Eckteil 1-UntenLinks.step, Eckteil 1-UntenLinks.stl, Eckteil 2-UntenRechts.step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]
2024-09-07 Add files via upload
    Stärke der Moosgummimatten von 2mm auf 3mm erhöht. Das senkt das Risiko, dass sich die Matten über die Zeit wellen und so eine unebene Unterlage entsteht.
    [Materialliste.xlsx]
2024-11-24 Add files via upload
    Nun habe ich endlich einen Lieferanten gefunden, der eine Moosgummimatte aus einem einzigen Stück in der notwendigen Grösse liefern kann. Die Anleitung und die Materialliste wurden entsprechend angep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
    [Materialliste.xlsx]
